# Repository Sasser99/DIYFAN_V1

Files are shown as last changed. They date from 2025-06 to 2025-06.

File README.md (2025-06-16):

# DIY-Fan-V1

Files from the YouTube video: **"DIY Fan V1 – I Built This Modular Open Source Project"**

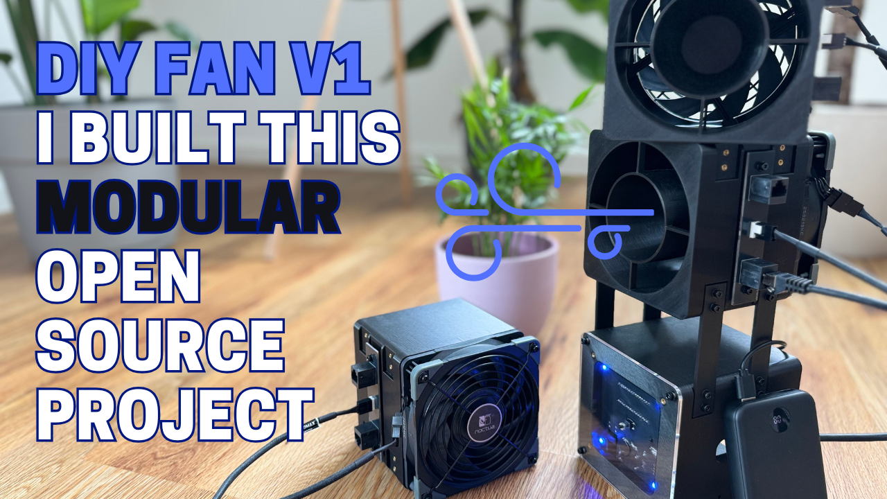
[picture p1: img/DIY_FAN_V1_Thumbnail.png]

https://www.youtube.com/watch?v=IbPePFFd2lk

## Project structure

- **ECAD/** – KiCad files  
- **CODE/** – Arduino code  
- **CAD/** – 3D models (STL, STEP)
- **BOM/** – Each assembly has its own BOM, organized in separate worksheets within a single .ods file.

## License

This project is open source and licensed as follows:

- **ECAD:** CERN Open Hardware License v2.0  
- **CODE:** MIT License  
- **CAD:** Creative Commons Attribution 4.0 (CC BY 4.0)

➡️ For full license texts, see the [LICENSE](LICENSE) file.

## Story

I came up with the idea to develop a modular, battery-powered, open-source fan built around high-end gaming PC fans. Gaming PC fans have low power consumption and, in the best case, are very quiet. Both are qualities that are also useful when the goal is not to cool PC components, but people. Additionally, the goal was to create a visually appealing and functional design.

The result is a system with **three main assemblies**: 

### 1. Fan Stage

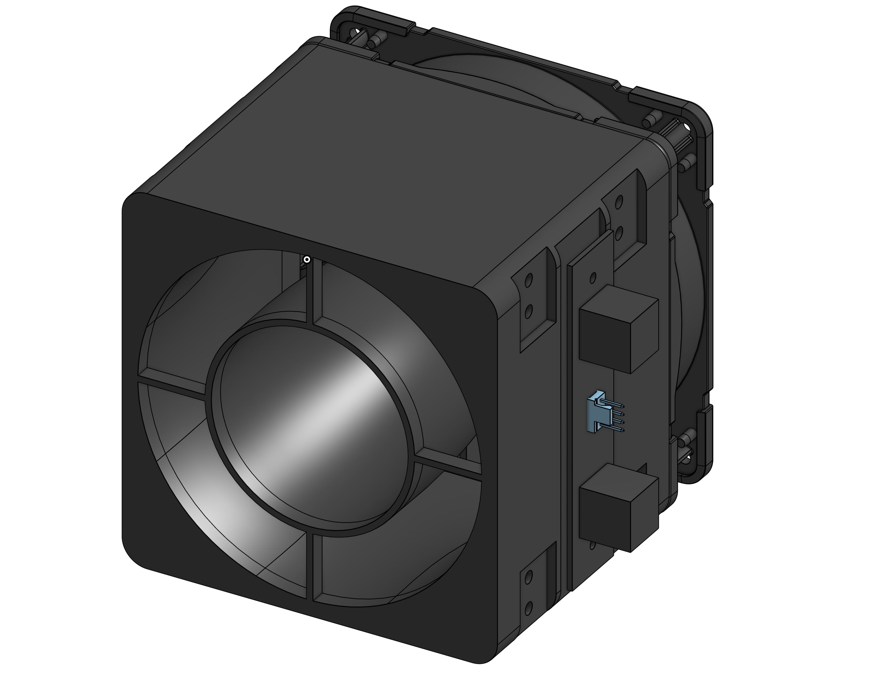
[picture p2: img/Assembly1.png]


- This assembly consists of three parts: a fan, the interface_V1 PCBA, and the shroud.
- I chose the **Noctua NF-A12x25 PWM chromax.black.swap**, which offers a solid balance between airflow and static pressure.
- Other fans can be used as long as they have similar characteristics (e.g., airflow and static pressure).
- The shroud **increases wind speed by around 80%**, allowing the fan to be placed further away while still being effective. More on this in the YouTube video! :)
- The interface_V1 PCBA is mounted on the side and connects to the fan, forwarding its signals.

### 2. Main Electronics Module

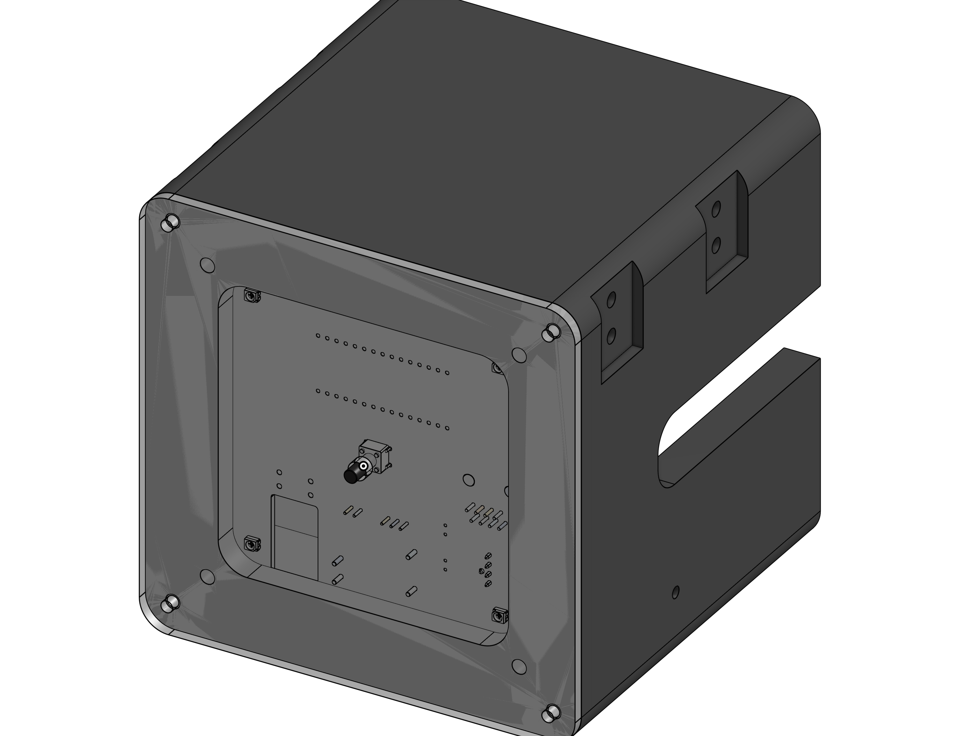
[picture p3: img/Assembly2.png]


- This module supplies approximately **10W** of power. With fans like the Noctua NF-A12x25, up to five fan stages can be powered simultaneously.
- A single **button** is used to cycle through PWM levels.
- Four **RGB LEDs**, visible through the plexiglass cover, indicate the active PWM level.

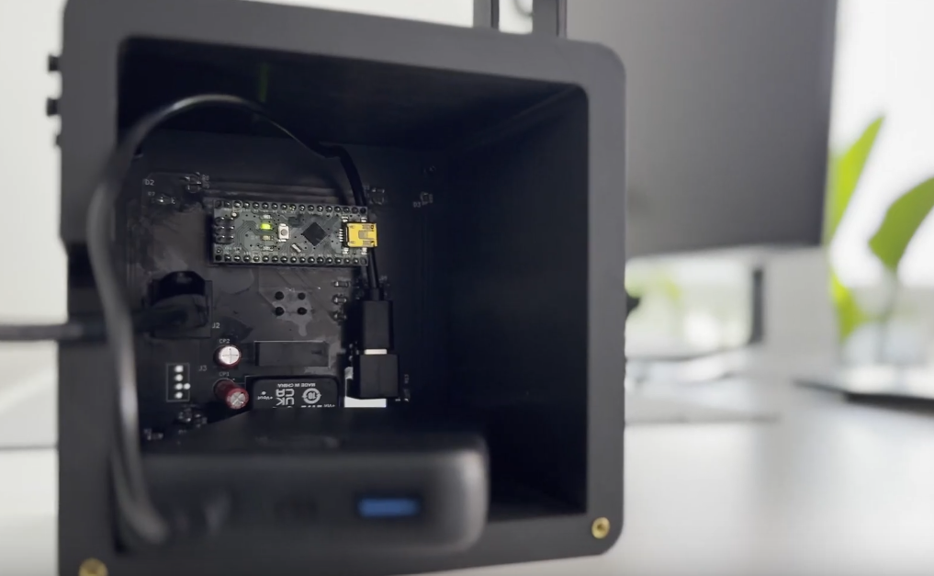
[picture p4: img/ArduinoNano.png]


- I chose the **Arduino Nano** because it's compact, easy to use via the Arduino IDE, and perfect for replicating the build—especially for those with Arduino experience.
- The Nano is mounted on a small **custom PCB** that also houses LEDs, DC-DC converters, and a few additional components. But don’t worry: the total component count remains very manageable.
- I also used a **15W power bank** instead of a custom battery to keep replication easy.

### 3. Tripod

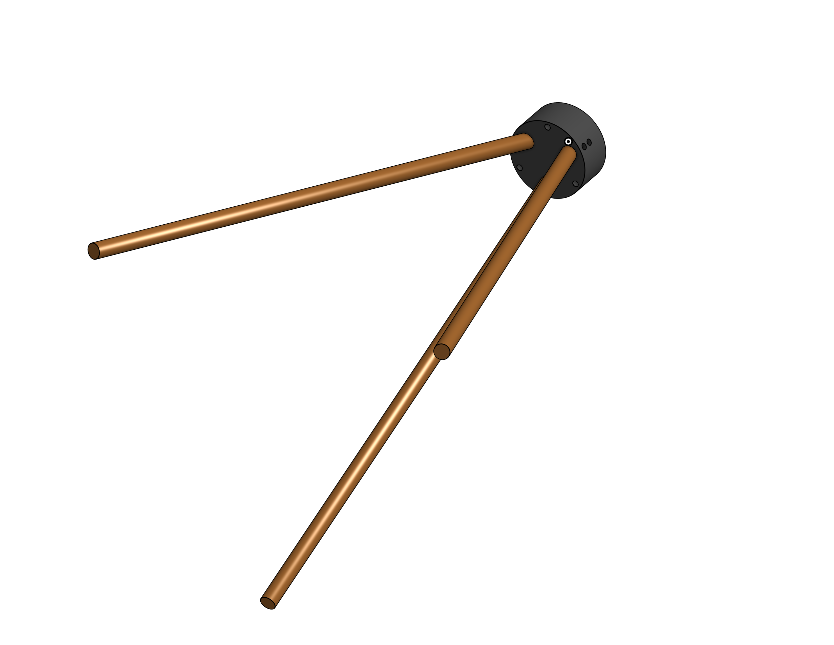
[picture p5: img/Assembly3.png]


- The tripod is simple but functional. If the legs are cut cleanly, the fan stands level.
- It provides the necessary stability, and I think the wood finish enhances the overall aesthetic.

### Configurations

The overall goal was to create a modular system. The three assemblies can be combined in different configurations using mechanical connectors and standard **Ethernet cables**, which transmit both power and PWM signal. The following configurations are demonstrated in the YouTube video:

**Full Build (with 3/5 Fans)**

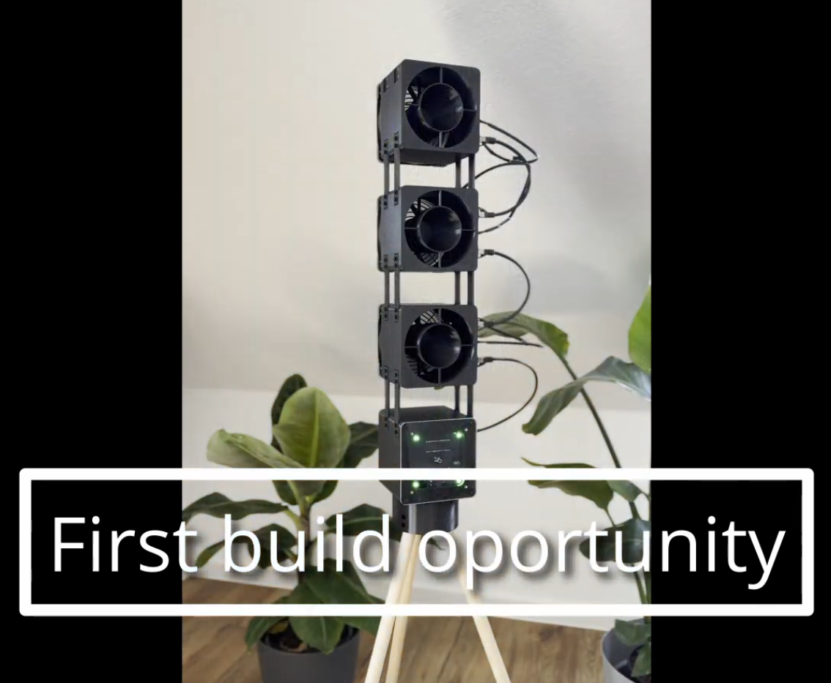
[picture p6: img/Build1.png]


**Desk Setup**

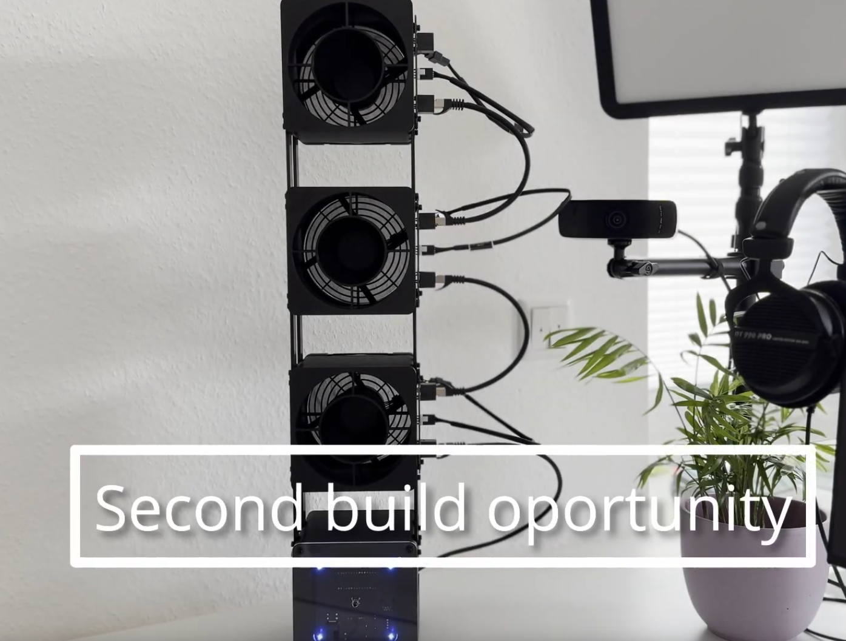
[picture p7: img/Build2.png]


**Split Mode (Left and Right → Stereo)**

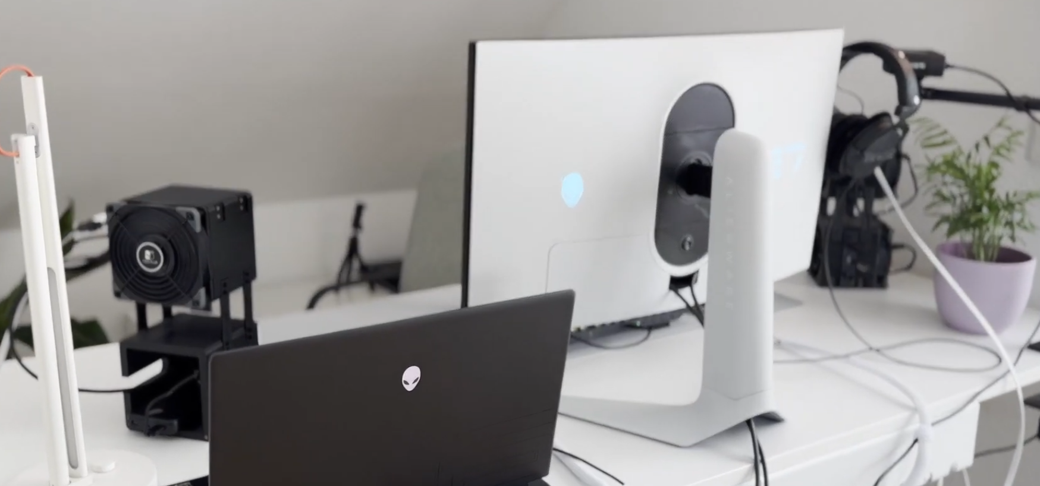
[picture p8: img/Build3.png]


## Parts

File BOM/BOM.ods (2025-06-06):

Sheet: Fan Stage
Component | Sub component | Quantity | Manufacturer Part Number | Link
DIYFAN_V1_Shroud.stl |  | 1
Noctua NF-A12x25 PWM chromax.black.swap |  | 1 |  | https://noctua.at/de/nf-a12x25-pwm-chromax-black-swap
PCBA: DIYFAN _interface_V1 |  | 1
 | Modular Connectors / Ethernet Connectors WR-MJ_8P8C_THT_Vertical | 2 | 615008160321 | https://www.mouser.de/ProductDetail/Wurth-Elektronik/615008160321?qs=OlC7AqGiEDmnhkTBXznxsQ%3D%3D
 | Headers & Wire Housings 4P VERT HDR W/FL | 1 | 47053-1000 | https://www.mouser.de/ProductDetail/Molex/47053-1000?qs=ph4zPCVRuvqoDX7hrEhxNA%3D%3D
 | PCB (see gerber) | 1
Ruthex M3 thread insert |  | 22 |  | https://www.ruthex.de/en/products/ruthex-gewindeeinsatz-m3-100-stuck-rx-m3x5-7-messing-gewindebuchsen
Screw M3 x 6 mm |  | Depends on connector quantity
Screw M3 x 30 mm |  | 4
M3 Washers |  | Min. 4
Noctua Fan-Grill |  | 1 | NA-FG1-12 | https://noctua.at/en/na-fg1-12
Network Cable (0.25 m as shown in the video build) |  | 1 |  | https://www.amazon.de/gp/product/B08HDJLJ9J?language=en_GB

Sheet: Main Electronics Module
Component | Sub component | Quantity | Manufacturer Part Number | Link
DIYFAN_V1_Electronic-Housing.stl |  | 1
DIYFAN_V1_Electronic-Housing-Cover.step |  | 1
PCBA: DIYFAN_V1 |  | 1
 | PCB (see gerber) | 1
 | Isolated DC/DC Converters - Through Hole 5Vin 5Vout 0-400mA 2W SIP Unreg Iso | 1 | SPUN02L-05 | https://www.mouser.de/ProductDetail/MEAN-WELL/SPUN02L-05
 | Isolated DC/DC Converters - Through Hole 4.7-9Vin 12Vout 833mA DIP Iso Reg | 1 | SKM10E-12 | https://www.mouser.de/ProductDetail/MEAN-WELL/SKM10E-12
 | Multi-Colour LEDs WL-SFTW SMT full-color TOP LED waterclear | 4 | 150141M173100 | https://www.mouser.de/ProductDetail/Wurth-Elektronik/150141M173100?qs=2kOmHSv6VfT%2Fmnpysgc7Ng%3D%3D
 | Short-stroke key 6x6 mm, height: 12.5 mm, 12 V, vert. | 1 | JTP-1130D | https://www.reichelt.com/de/en/shop/product/short-stroke_key_6x6_mm_height_12_5_mm_12_v_vert_-27894
 | Arduino Nano | 1 | SKU A000005 | https://store.arduino.cc/products/arduino-nano
 | Aluminium Electrolytic Capacitors - Radial Leaded WCAP-ATG8 100uF 35V 20% Radial | 2 | 860010573007 | https://www.mouser.de/ProductDetail/Wurth-Elektronik/860010573007
 | Bipolar Transistors - BJT LO V NPN TRANSISTOR 40V 4.0A | 6 | NSS40201LT1G | https://www.mouser.de/ProductDetail/onsemi/NSS40201LT1G?qs=JZRcihQa5buDxAwNVotiBw%3D%3D
 | USB Connectors USB TYPE C | 1 | 10164359-00011LF | https://www.mouser.de/ProductDetail/Amphenol-FCI/10164359-00011LF?qs=MyNHzdoqoQLpQ%2FmSqA1%252BtQ%3D%3D
 | Modular Connectors / Ethernet Connectors WR-MJ_8P8C_THT_Vertical | 1 | 615008160321 | https://www.mouser.de/ProductDetail/Wurth-Elektronik/615008160321?qs=OlC7AqGiEDmnhkTBXznxsQ%3D%3D
 | female connector 2,54mm, 1x16, separable, gold plated | 2 | BL1.16 G | https://www.reichelt.com/de/en/shop/product/female_connector_2_54mm_1x16_separable_gold_plated-283786
 | Resistor 3KOhm 1206 | 3
 | Resistor 90Ohm 1206 | 8
 | Resistor 150Ohm 1206 | 4
Ruthex M3 thread insert |  | 19 |  | https://www.ruthex.de/en/products/ruthex-gewindeeinsatz-m3-100-stuck-rx-m3x5-7-messing-gewindebuchsen
Screw M3 x 6 mm |  | Depends on
Network Cable Network Cable (0.5 m as shown in the video build) |  | 1 |  | https://www.amazon.de/gp/product/B08HDG8GV2/ref=ox_sc_act_title_1?th=1&language=en_GB

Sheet: Tripod
Component | Sub component | Quantity | Manufacturer Part Number | Link
DIYFAN_V1_Tripod.stl |  | 1
DIYFAN_V1_Stick.step |  | 3
Screw M3 x 8 mm |  | 3
Wood Screw 3,5x30 |  | 6

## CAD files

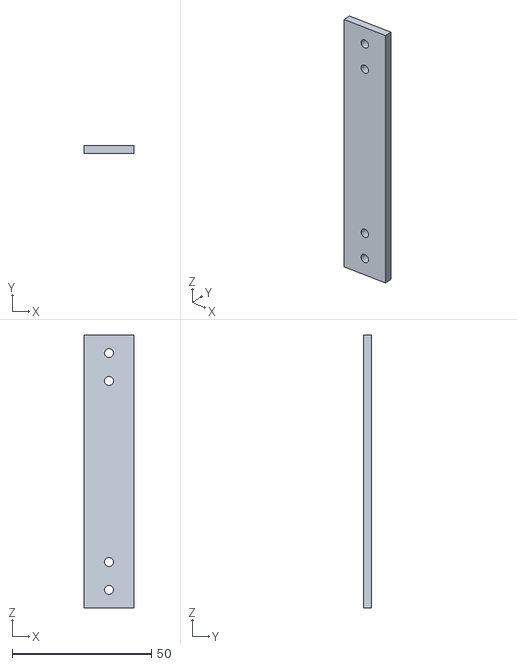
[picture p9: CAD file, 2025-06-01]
CAD/DIYFAN_V1_Connector.stl
18.0 x 3.00 x 98.0

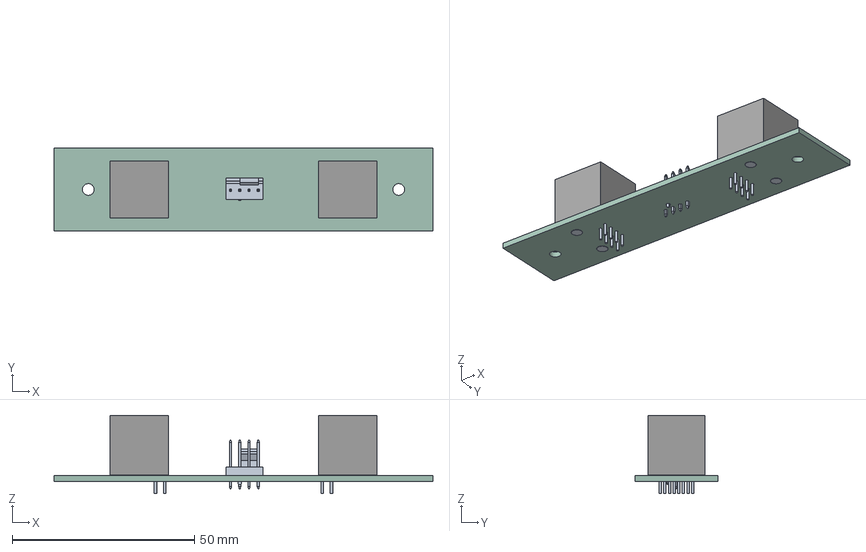
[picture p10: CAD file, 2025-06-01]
ECAD/DIYFAN _interface_V1/DIYFAN _interface_V1.step
103.9 x 22.9 x 21.4 mm
ASSEMBLY x 2
DIYFAN _interface_V1_PCB

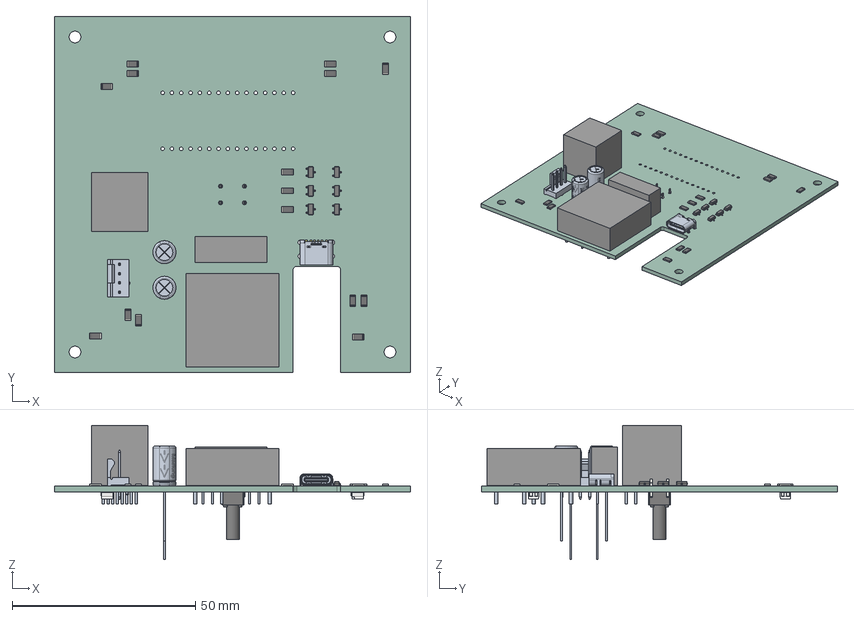
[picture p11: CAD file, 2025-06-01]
ECAD/DIYFAN_V1/DIYFAN_V1.step
97.0 x 97.0 x 36.5 mm
R_1206_3216Metric x 15
10164359-00011LF
ASSEMBLY x 3
SOT-23-3 x 6
CP_Wurth_WCAP-ATG8-P2.5D6.3L11 x 2
150141M173100 x 4
SW_PUSH_6mm_h13mm
DIYFAN_V1_PCB

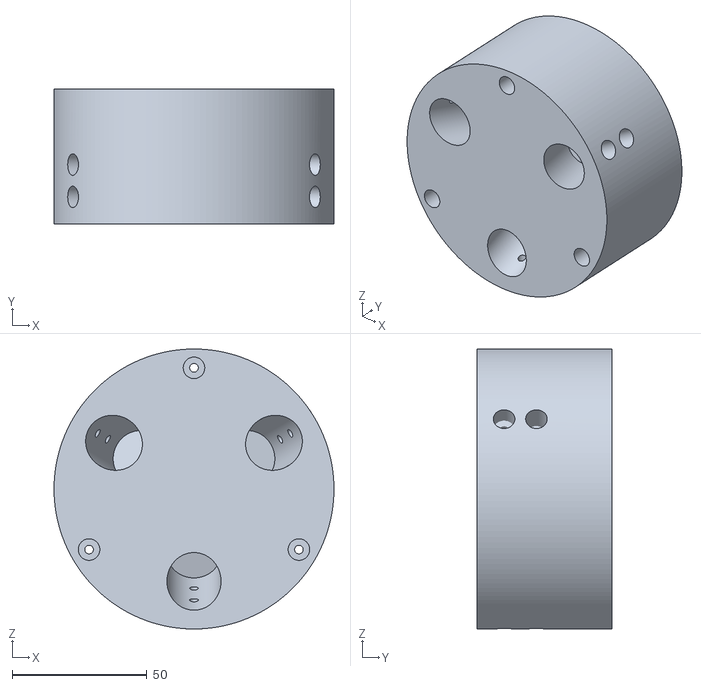
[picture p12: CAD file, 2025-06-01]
CAD/DIYFAN_V1_Tripod.stl
104.0 x 50.0 x 104.0

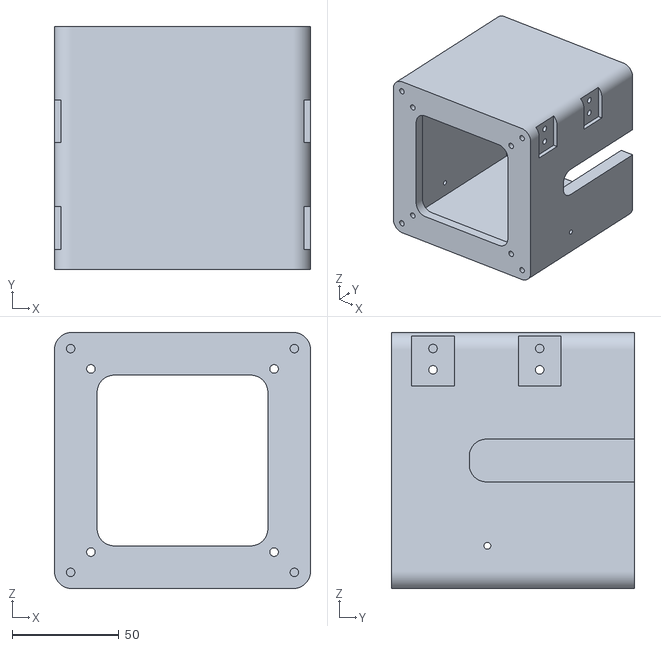
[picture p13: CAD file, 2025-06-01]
CAD/DIYFAN_V1_Electronic-Housing.stl
120.0 x 114.0 x 120.0

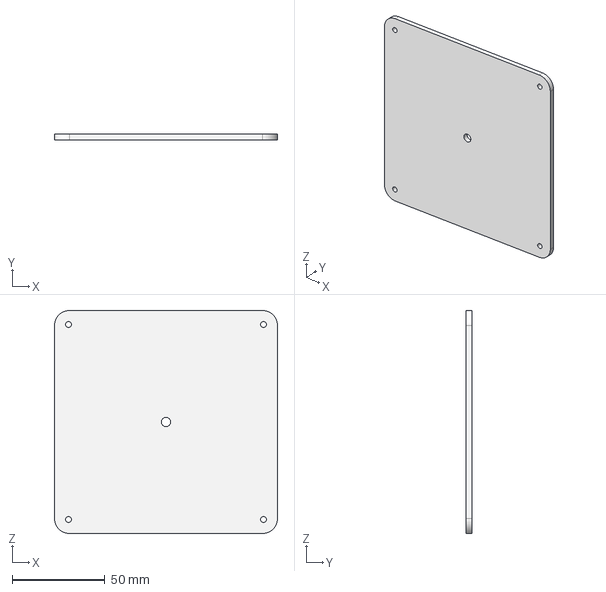
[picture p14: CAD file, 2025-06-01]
CAD/DIYFAN_V1_Electronic-Housing-Cover.step
120.0 x 3.00 x 120.0 mm

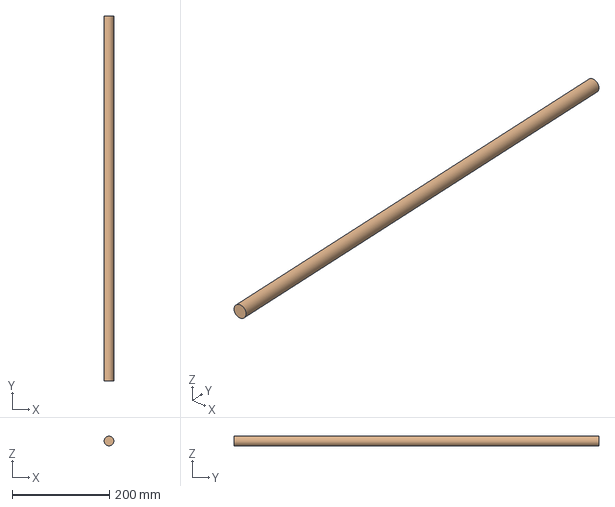
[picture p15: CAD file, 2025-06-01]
CAD/DIYFAN_V1_Stick.step
20.0 x 750.0 x 20.0 mm

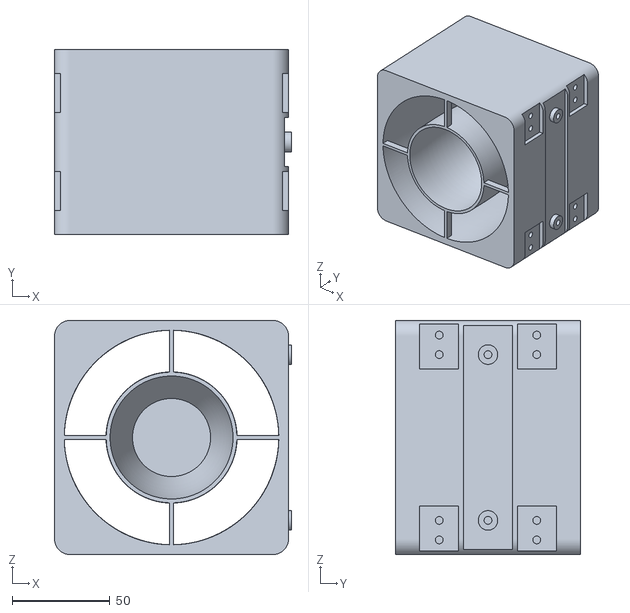
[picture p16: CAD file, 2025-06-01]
CAD/DIYFAN_V1_Shroud.stl
121.5 x 95.0 x 120.0

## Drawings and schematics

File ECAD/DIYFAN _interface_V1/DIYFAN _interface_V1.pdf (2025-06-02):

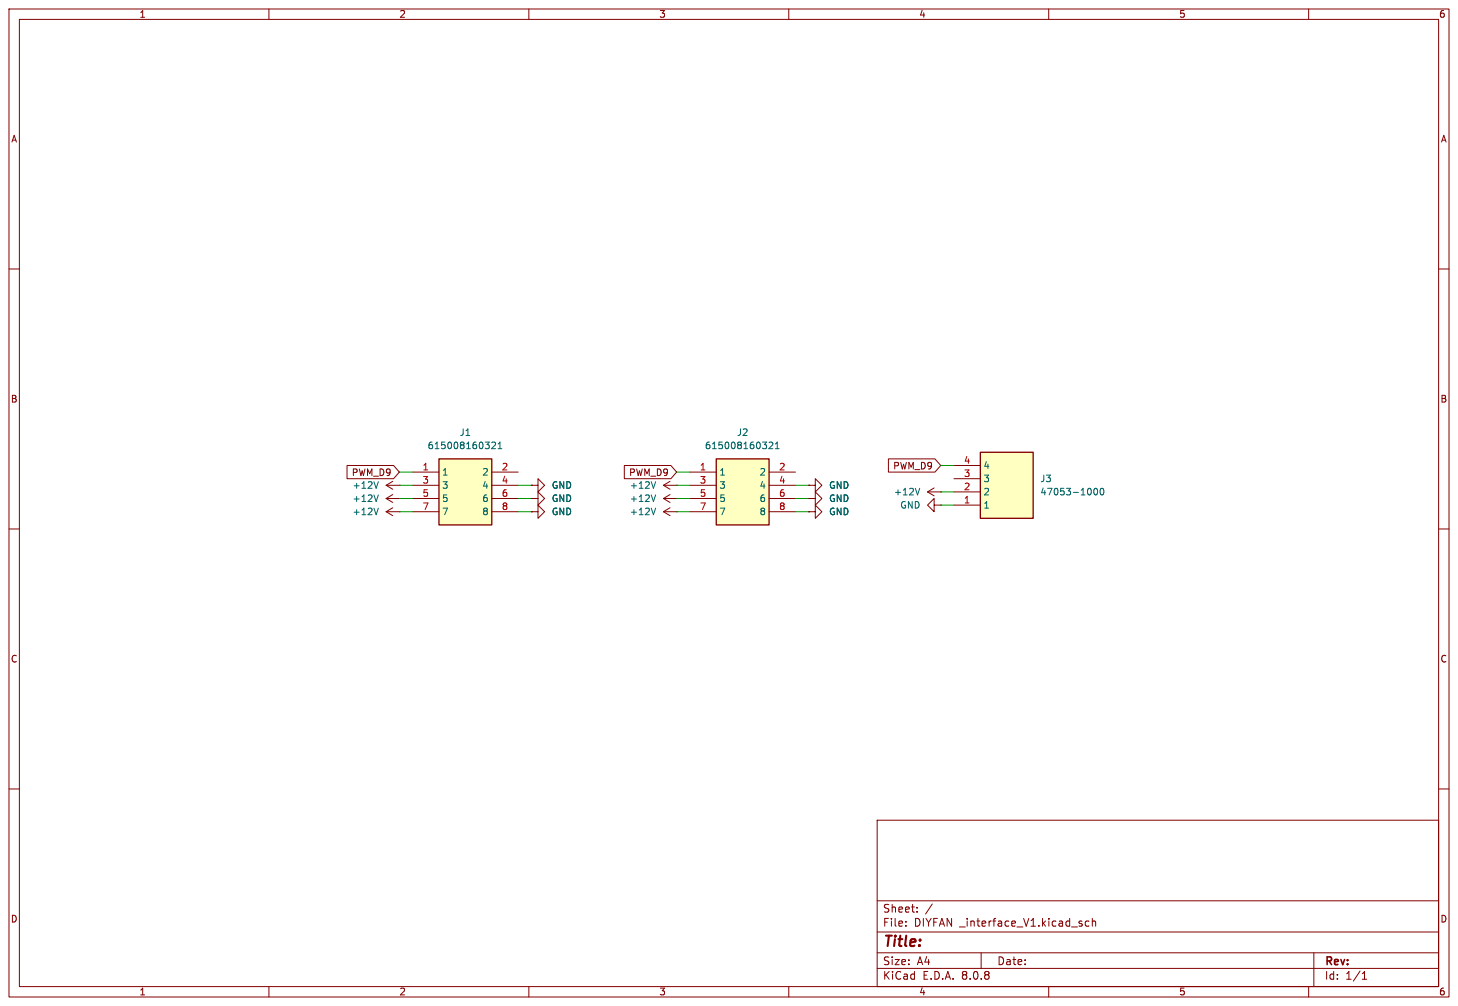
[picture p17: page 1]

Id: 1/1 Title: File: DIYFAN _interface_V1.kicad_sch Sheet: /

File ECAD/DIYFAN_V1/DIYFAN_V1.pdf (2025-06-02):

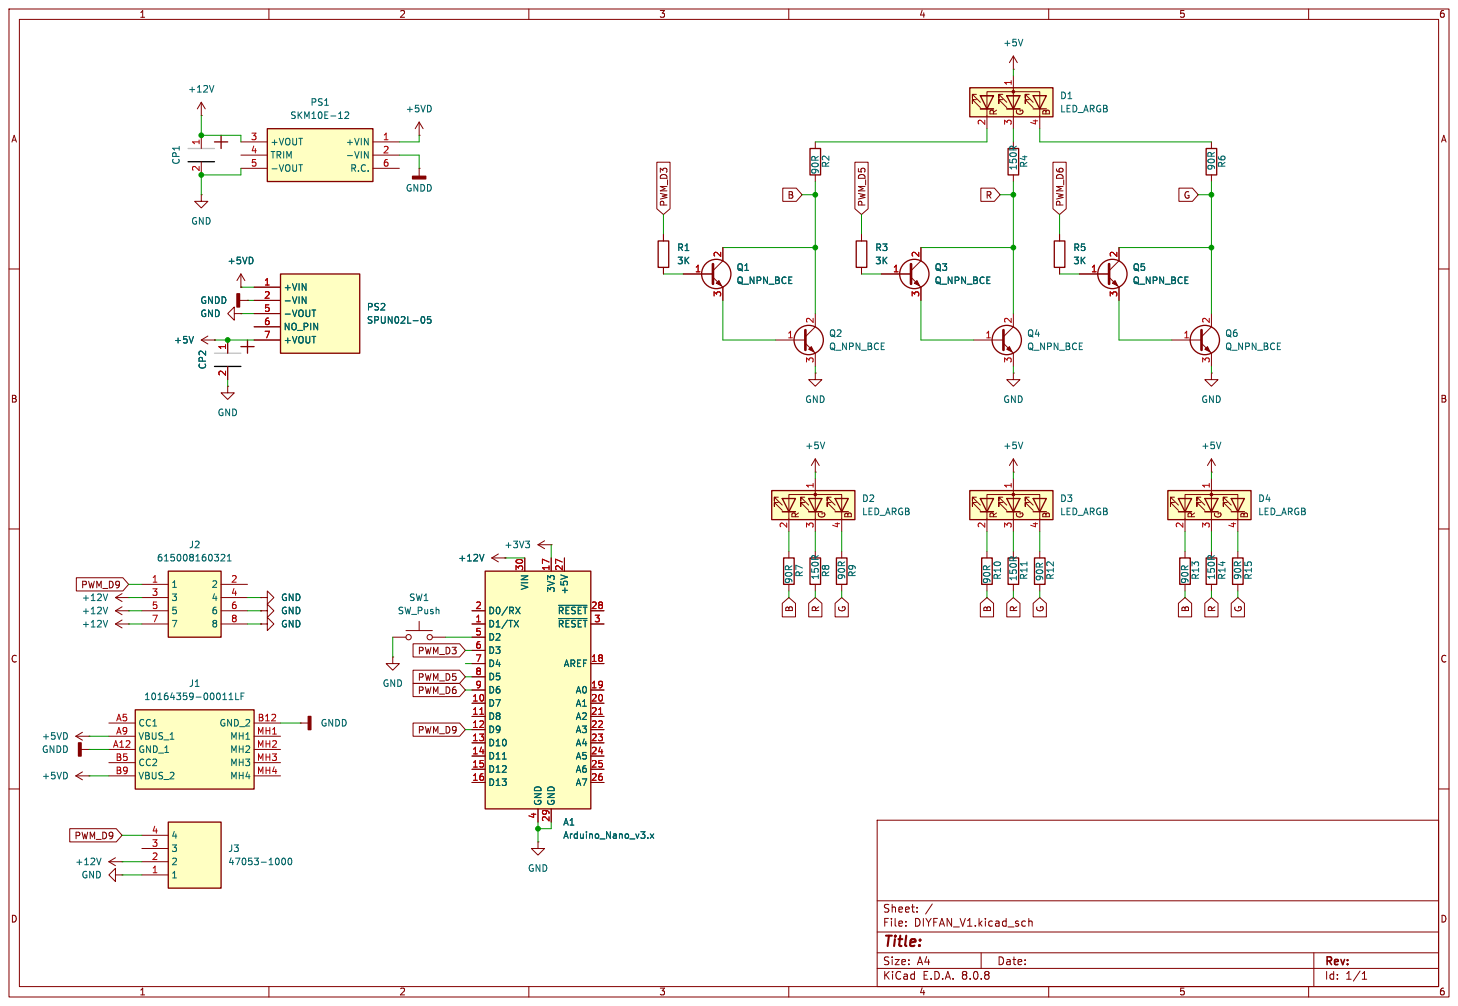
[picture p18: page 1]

2 3 Q4 Q_NPN_BCE GND GND GNDD GND GND GND
615008160321 GND

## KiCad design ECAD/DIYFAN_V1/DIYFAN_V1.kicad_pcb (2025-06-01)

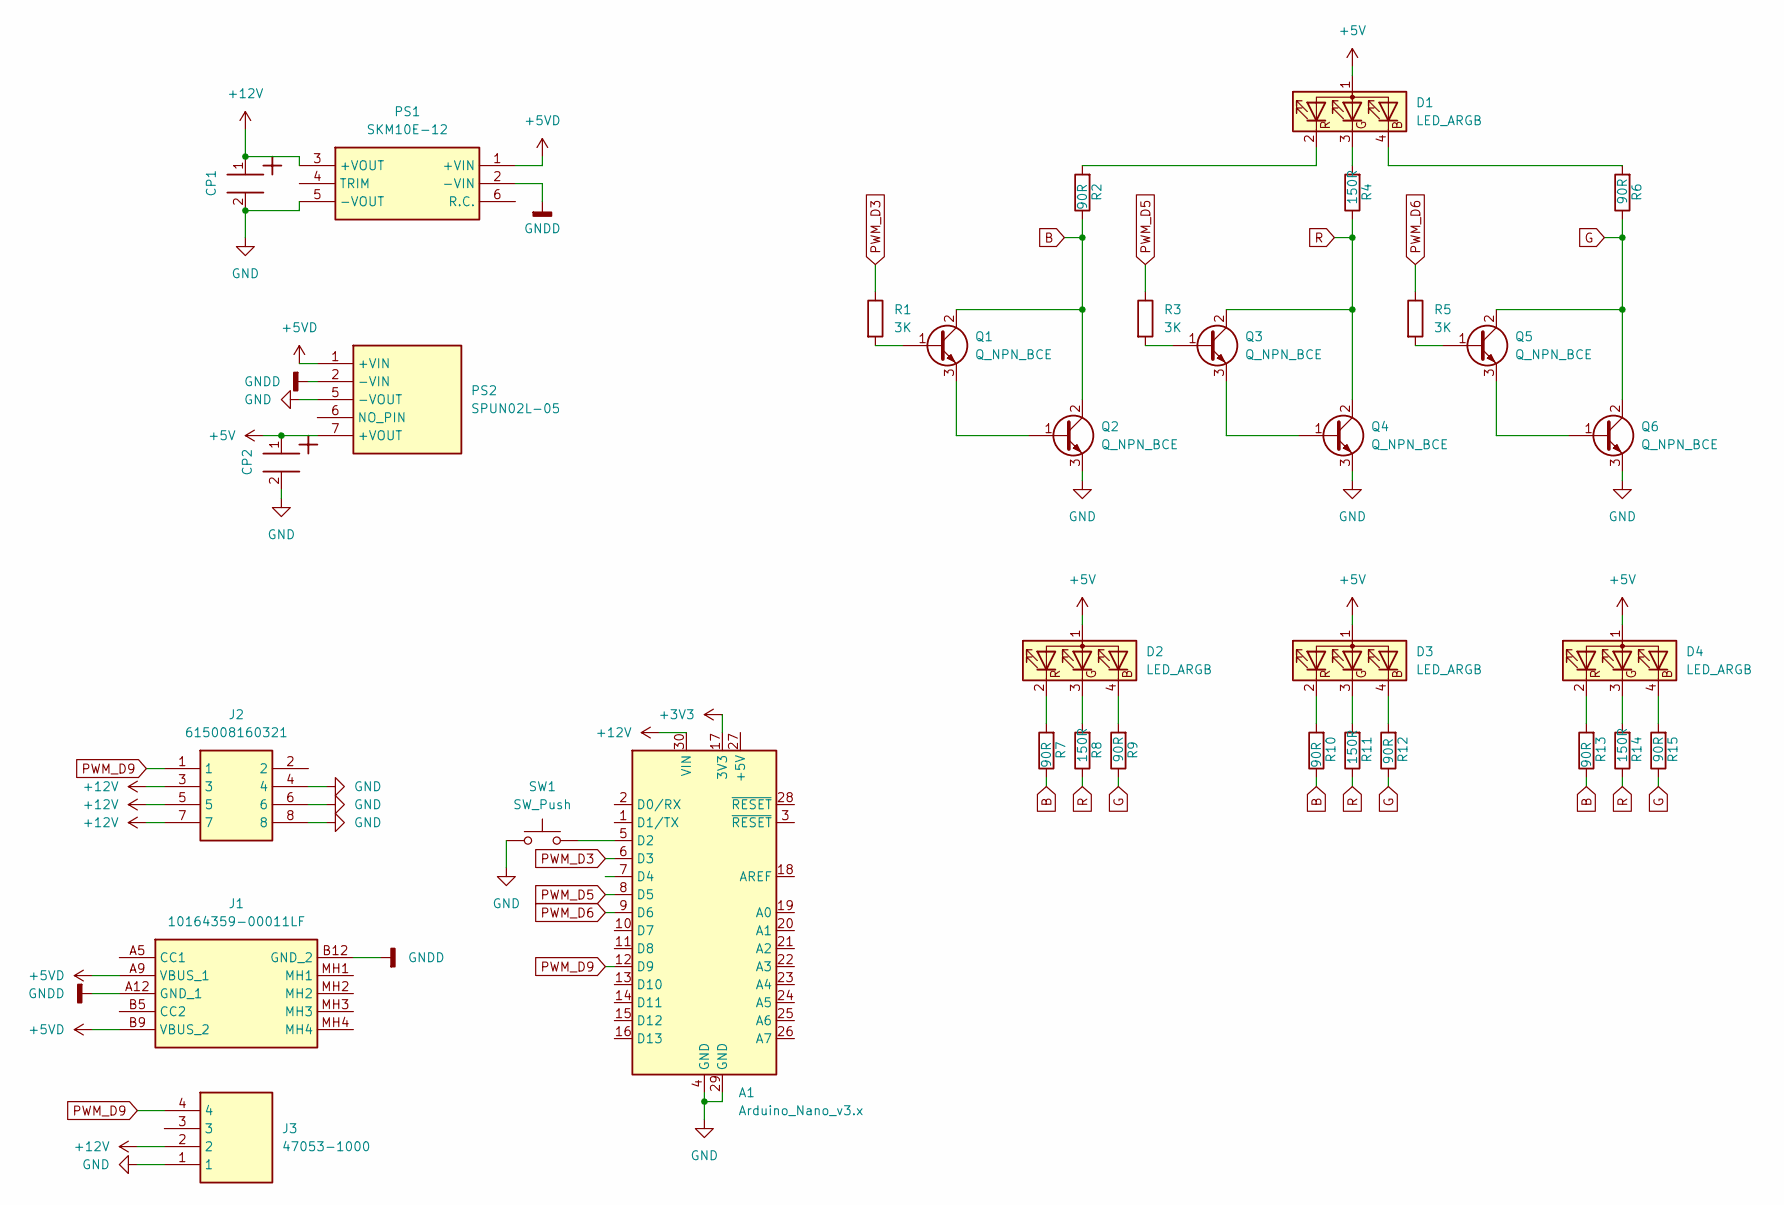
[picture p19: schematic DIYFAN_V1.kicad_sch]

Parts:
A1: Arduino_Nano_v3.x; Arduino_Nano
CP1, CP2: P2.5D6.3L11_860010573007_Modified; CP_Wurth_WCAP-ATG8-P2.5D6.3L11; Part Number 860010573007
D1, D2, D3, D4: LED_ARGB; 150141M173100
J1: 10164359-00011LF; 1016435900011LF_handsoldered; Mouser Part Number 649-10164359-00011LF
J2: 615008160321; Mouser Part Number 710-615008160321
J3: 47053-1000; 470531000; Mouser Part Number 538-47053-1000
PS1: SKM10E-12; SKM10B05; Mouser Part Number 709-SKM10E-12
PS2: SPUN02L-05; SPUN02L05; Mouser Part Number 709-SPUN02L-05
Q1, Q2, Q3, Q4, Q5, Q6: Q_NPN_BCE; SOT-23-3
R1, R3, R5: 3K; R_1206_3216Metric_Pad1.30x1.75mm_HandSolder
R2, R6, R7, R9, R10, R12, R13, R15: 90R; R_1206_3216Metric_Pad1.30x1.75mm_HandSolder
R4, R8, R11, R14: 150R; R_1206_3216Metric_Pad1.30x1.75mm_HandSolder
SW1: SW_Push; SW_PUSH_6mm_H13mm

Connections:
+3V3: A1.17 (3V3)
+5V: CP2.1, D1.1 (A), D2.1 (A), D3.1 (A), D4.1 (A), PS2.7 (+VOUT)
+5VD: J1.A9 (VBUS_1), J1.B9 (VBUS_2), PS1.1 (+VIN), PS2.1 (+VIN)
+12V: A1.30 (VIN), CP1.1, J2.3, J2.5, J2.7, J3.2, PS1.3 (+VOUT)
B: Q1.2 (C), Q2.2 (C), R2.1, R7.1, R10.1, R13.1
G: Q5.2 (C), Q6.2 (C), R6.1, R9.1, R12.1, R15.1
GND: A1.4 (GND), A1.29 (GND), CP1.2, CP2.2, J2.4, J2.6, J2.8, J3.1, PS1.5 (-VOUT), PS2.5 (-VOUT), Q2.3 (E), Q4.3 (E), Q6.3 (E), SW1.1
GNDD: J1.A12 (GND_1), J1.B12 (GND_2), PS1.2 (-VIN), PS2.2 (-VIN)
unnamed: A1.5 (D2), SW1.2
unnamed: D1.4 (BK), R6.2
unnamed: D1.3 (GK), R4.2
unnamed: D1.2 (RK), R2.2
unnamed: D2.4 (BK), R9.2
unnamed: D2.3 (GK), R8.2
unnamed: D2.2 (RK), R7.2
unnamed: D3.4 (BK), R12.2
unnamed: D3.3 (GK), R11.2
unnamed: D3.2 (RK), R10.2
unnamed: D4.4 (BK), R15.2
unnamed: D4.3 (GK), R14.2
unnamed: D4.2 (RK), R13.2
unnamed: Q1.1 (B), R1.2
unnamed: Q1.3 (E), Q2.1 (B)
unnamed: Q3.1 (B), R3.2
unnamed: Q3.3 (E), Q4.1 (B)
unnamed: Q5.1 (B), R5.2
unnamed: Q5.3 (E), Q6.1 (B)
PWM_D3: A1.6 (D3), R1.1
PWM_D5: A1.8 (D5), R3.1
PWM_D6: A1.9 (D6), R5.1
PWM_D9: A1.12 (D9), J2.1, J3.4
R: Q3.2 (C), Q4.2 (C), R4.1, R8.1, R11.1, R14.1

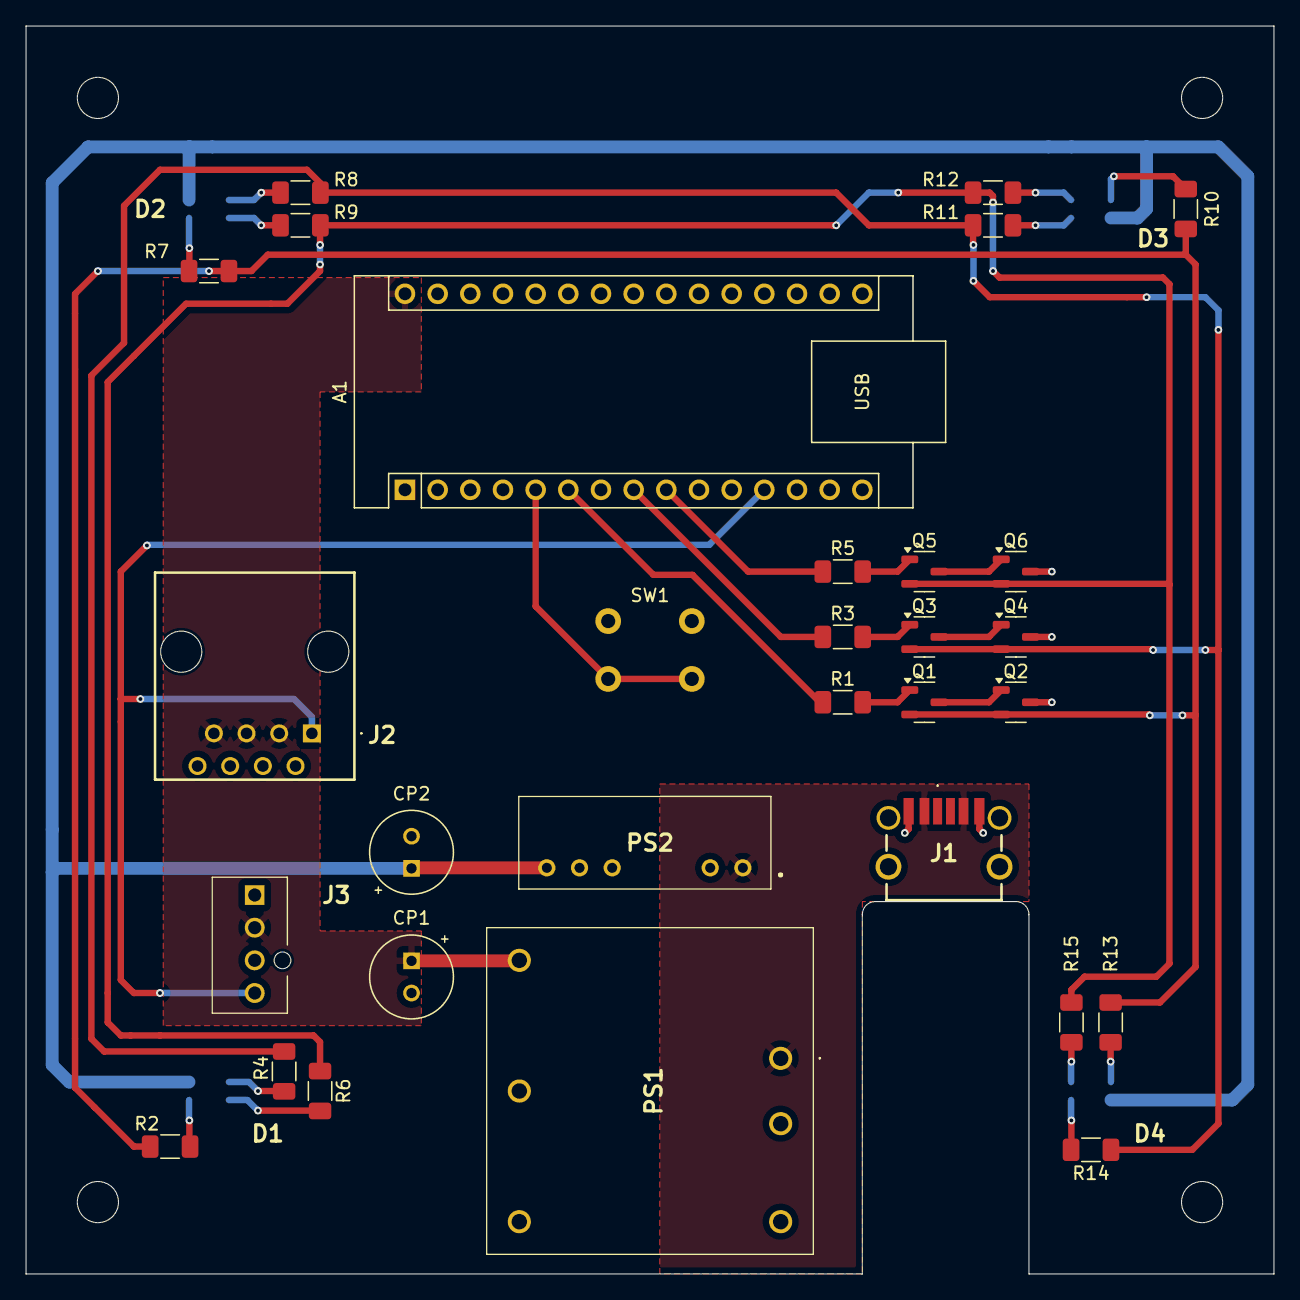
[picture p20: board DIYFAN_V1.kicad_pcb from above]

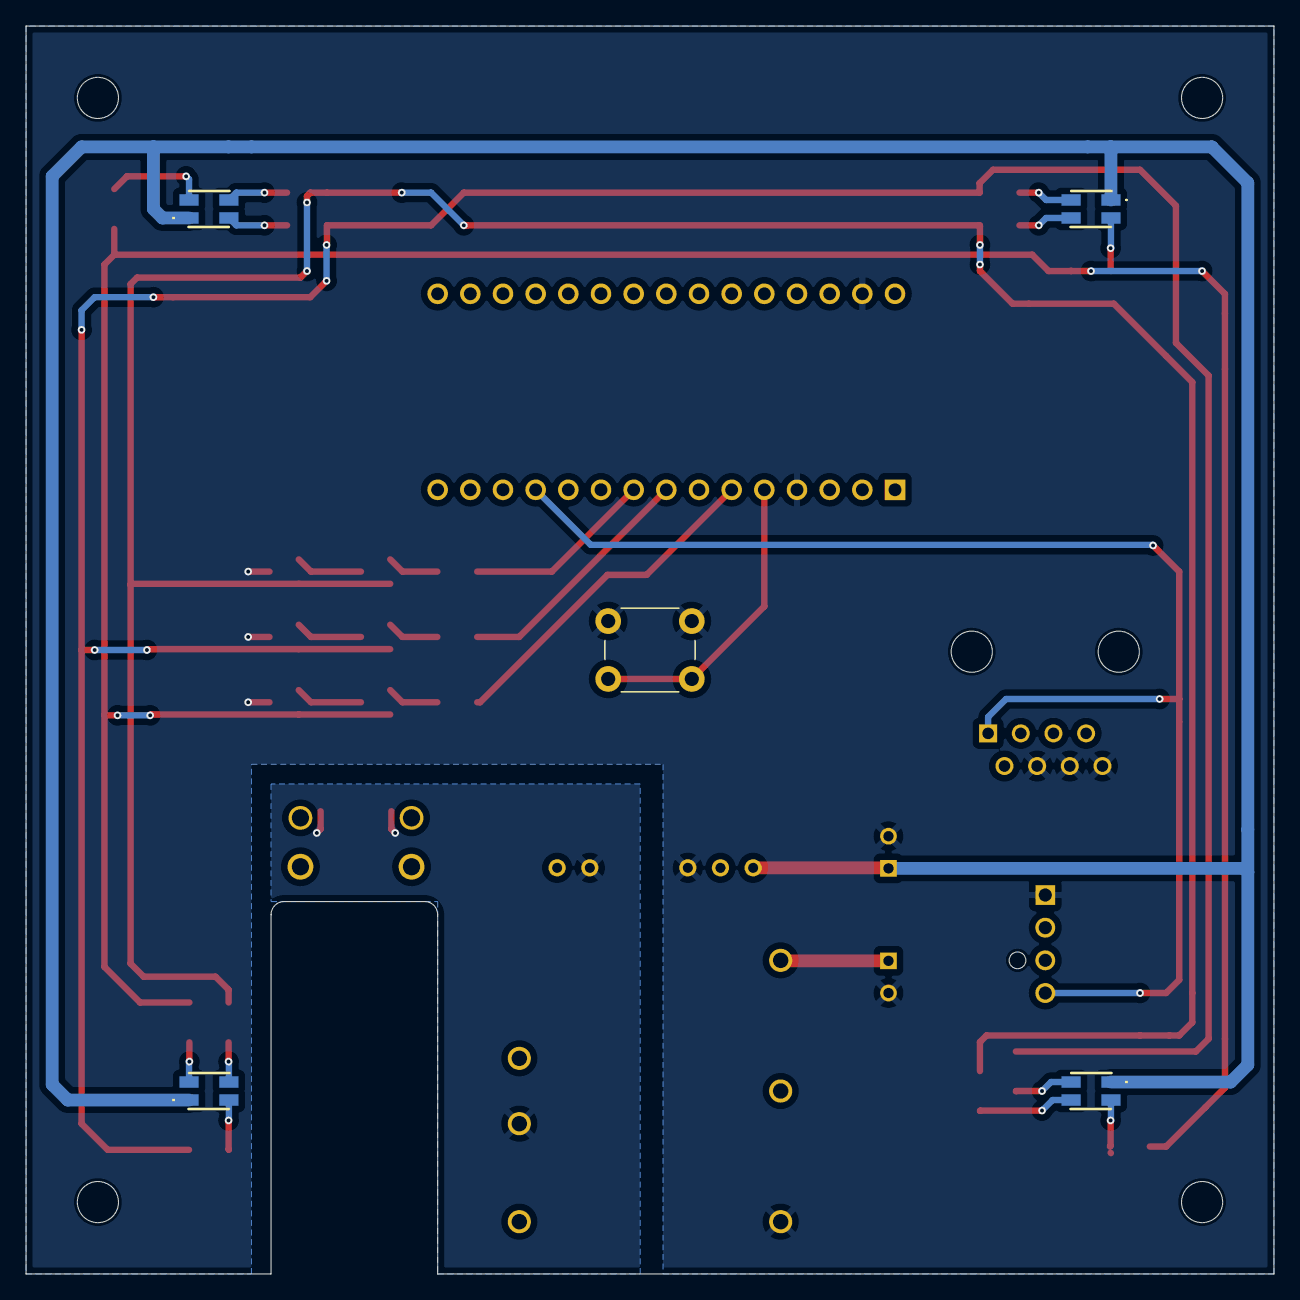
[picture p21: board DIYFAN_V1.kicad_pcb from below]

Board: 2 copper layers, 97.0 x 97.0 mm, 34 parts (5 on the bottom side), 31 nets.

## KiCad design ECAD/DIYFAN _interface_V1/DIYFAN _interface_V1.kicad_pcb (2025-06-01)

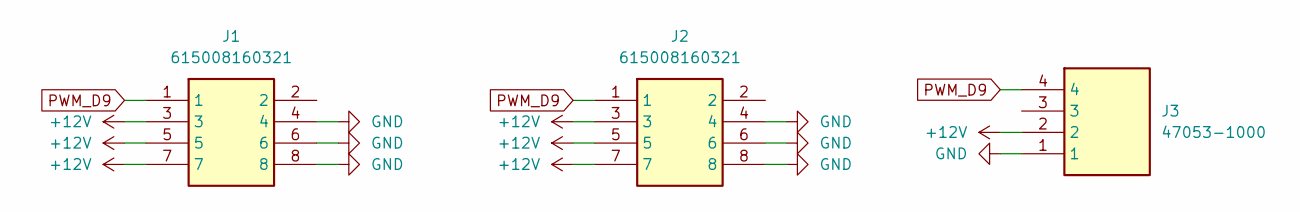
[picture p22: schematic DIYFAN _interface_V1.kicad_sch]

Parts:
J1, J2: 615008160321; Mouser Part Number 710-615008160321
J3: 47053-1000; 470531000; Mouser Part Number 538-47053-1000

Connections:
+12V: J1.3, J1.5, J1.7, J2.3, J2.5, J2.7, J3.2
GND: J1.4, J1.6, J1.8, J2.4, J2.6, J2.8, J3.1
PWM_D9: J1.1, J2.1, J3.4

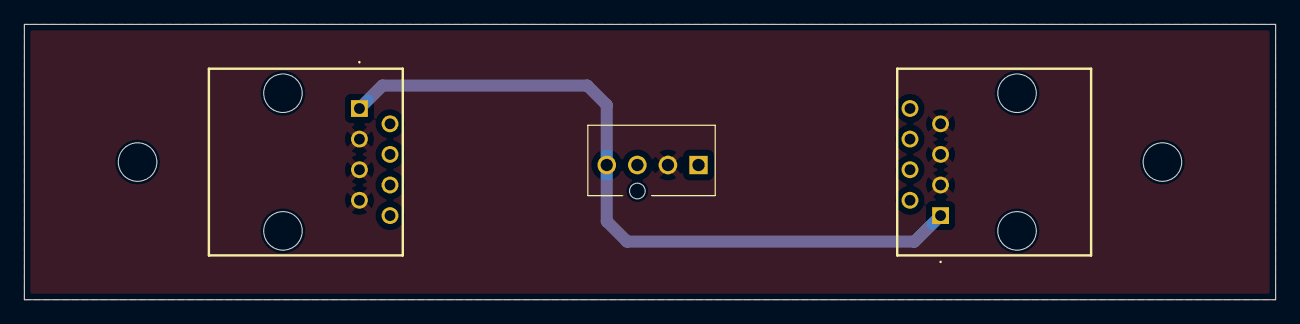
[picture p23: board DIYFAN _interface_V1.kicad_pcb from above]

Board: 2 copper layers, 103.9 x 22.9 mm, 3 parts (0 on the bottom side), 3 nets.

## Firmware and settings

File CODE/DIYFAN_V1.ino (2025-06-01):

const byte OC1A_PIN = 9;  // Pin for PWM output (D9)
const byte BUTTON_PIN = 2; // Button connected to pin D2
const byte RED_PIN = 5;    // Red channel of the RGB LED (D3)
const byte GREEN_PIN = 6;  // Green channel of the RGB LED (D5)
const byte BLUE_PIN = 3;   // Blue channel of the RGB LED (D6)

const word PWM_FREQ_HZ = 25000; // PWM frequency
const word TCNT1_TOP = 16000000 / (2 * PWM_FREQ_HZ); // Timer value calculation

// The three PWM levels (33%, 66%, 100%)
const byte PWM_STAGES[3] = {33, 66, 100};
byte currentStage = 0; // Start with level 1 (index 0, i.e. 33%)

void setup() {
  pinMode(OC1A_PIN, OUTPUT); // Set pin D9 as output
  pinMode(BUTTON_PIN, INPUT_PULLUP); // Enable internal pull-up resistor on pin D2

  pinMode(RED_PIN, OUTPUT);   // Set pin D5 as output for red
  pinMode(GREEN_PIN, OUTPUT); // Set pin D6 as output for green
  pinMode(BLUE_PIN, OUTPUT);  // Set pin D3 as output for blue

  // Initialize Timer1
  TCCR1A = 0;
  TCCR1B = 0;
  TCNT1 = 0;

  // Configure Timer1 (Phase Correct PWM)
  TCCR1A |= (1 << COM1A1) | (1 << WGM11);  // Clear on compare match, Phase correct PWM
  TCCR1B |= (1 << WGM13) | (1 << CS10);    // Phase correct PWM, no prescaler
  ICR1 = TCNT1_TOP;  // Set top value for timer

  // Set PWM to the first level (33%)
  setPwmDuty(PWM_STAGES[currentStage]);
  // Set RGB LED to initial value (pulsing white)
  setRgbColor(currentStage);
}

void loop() {
  // Check if the button was pressed
  if (digitalRead(BUTTON_PIN) == LOW) {
    delay(50); // Debounce delay
    if (digitalRead(BUTTON_PIN) == LOW) { // Confirm button press
      // Select next PWM level
      currentStage = (currentStage + 1) % 3; // Cycle through levels
      setPwmDuty(PWM_STAGES[currentStage]);
      setRgbColor(currentStage);  // Adjust RGB LED to new level
    }
  }
}

// Function to set PWM duty cycle
void setPwmDuty(byte duty) {
  OCR1A = (word)(duty * TCNT1_TOP) / 100; // Set OCR1A for corresponding PWM duty
}

// Function to set RGB LED color based on PWM stage
void setRgbColor(byte stage) {
  switch (stage) {
    case 0: // Stage 1
      pulseRgb(0, 0, 255); // Blue
      break;
    case 1: // Stage 2
      pulseRgb(0, 255, 0); // Green
      break;
    case 2: // Stage 3 
      pulseRgb(0, 255, 255); // cyan
      break;
  }
}

// Function to pulse the RGB LED
void pulseRgb(byte red, byte green, byte blue) {
  for (int i = 0; i < 255; i++) {  // PWM value from 0 to 255
    analogWrite(RED_PIN, red * i / 255);   // Pulse red light
    analogWrite(GREEN_PIN, green * i / 255); // Pulse green light
    analogWrite(BLUE_PIN, blue * i / 255);  // Pulse blue light
    delay(10); // Short delay for pulsing
  }
  for (int i = 255; i > 30; i--) {
    analogWrite(RED_PIN, red * i / 255);   // Pulse red light
    analogWrite(GREEN_PIN, green * i / 255); // Pulse green light
    analogWrite(BLUE_PIN, blue * i / 255);  // Pulse blue light
    delay(10); // Short delay for pulsing
  }
}

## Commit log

2025-06-02 some modifications
    [BOM.ods]
2025-06-02 further changes
    [BOM.ods]
2025-06-02 added csv BOMs
    [Assembly_Fan-Stage.csv, Assembly_MainPCBA-Housing.csv, Assembly_Tripod.csv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]
2025-06-02 added story
    [BOM.ods]
2025-06-06 changed BOM
    [BOM.ods]
